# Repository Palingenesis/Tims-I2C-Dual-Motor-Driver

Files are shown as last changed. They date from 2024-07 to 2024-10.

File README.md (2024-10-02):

# This is My I2C Dual Motor Driver  
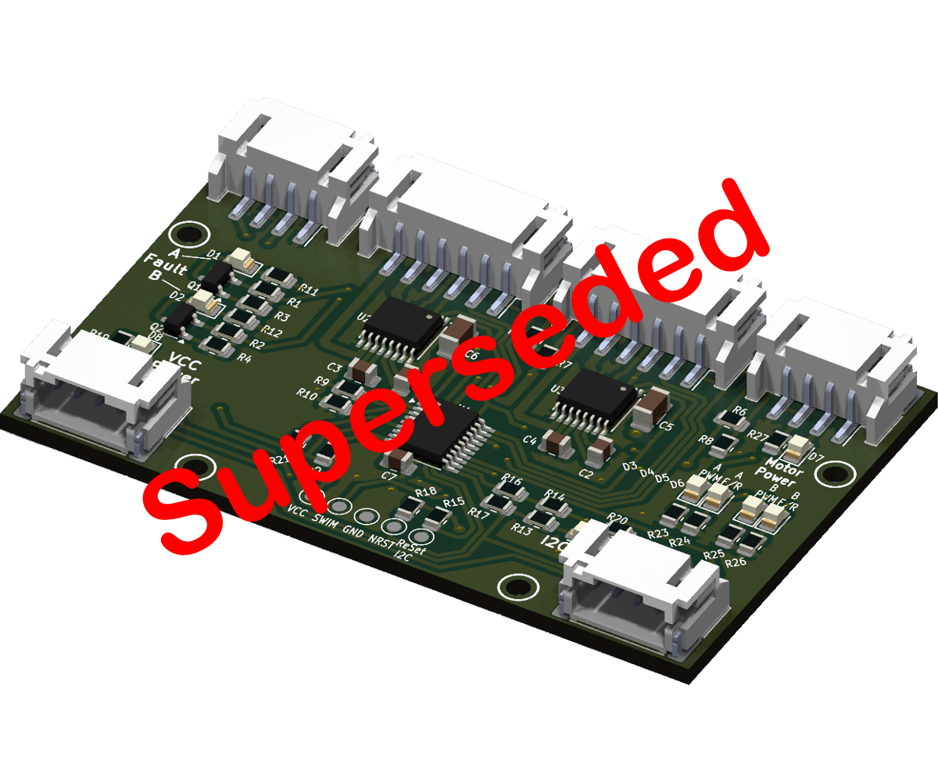
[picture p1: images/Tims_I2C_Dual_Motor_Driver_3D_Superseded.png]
3D Top
  
## This is an I2C controlled Dual Motor Driver Board.  
### This Board has been superseded by this one <a href="https://www.pcbway.com/project/shareproject/Tim_s_I2C_Dual_Motor_Driver_[Version_2]_0646aaaf.html">Tims I2C Dual Motor Driver Version 2</a>  
### Files are for [KiCAD EDA](https://www.kicad.org/)  
There is <span style="font-size: large;">**"Tims_I2C_Dual_Motor_Driver.kicad_pcb.zip"**</span> file  
* This can be used when **"Plot Files"** asked for at 
<sub></sub> 
when ordering 10 PCBs for $5  
* If you have <span style="font-size: large;">**[KiCAD EDA](https://www.kicad.org/)**</span>,  
<sub></sub>
have a Plugin Plugin that will make things simple to order a PCB,  
just load this project into <span style="font-size: large;">**[KiCAD EDA](https://www.kicad.org/)**</span> install the plugin click the Icon Plugin and it will create all the nesesery files needed and take you to order a PCB 
and compeate the form on 
<sub></sub> 
web site.  
  
<a href="https://www.pcbway.com/project/member/?bmbno=3B5E17AE-462C-47">PCB from PCBWay</a>
## About  
The board can control two motors with quadratic encoders and a station to set a reference point.  
This is my second I2C Motor Driver, My first worked OK, but The MOSFETS I used where a little temperamental,  
so I decided to make a more robust version.  
This one I decided to control 2 motors from one microcontroller.  
* The main reason for having it control two motors at the same time was that I tried my original motor drivers controlling a tracked vehicle.  
It worked fine with two single motor drivers  but because I was using a web interface to control them there was a delay between turning on/off each motor.  
* I thought having a motor driver that controls two motor at the same time was a better approach.  
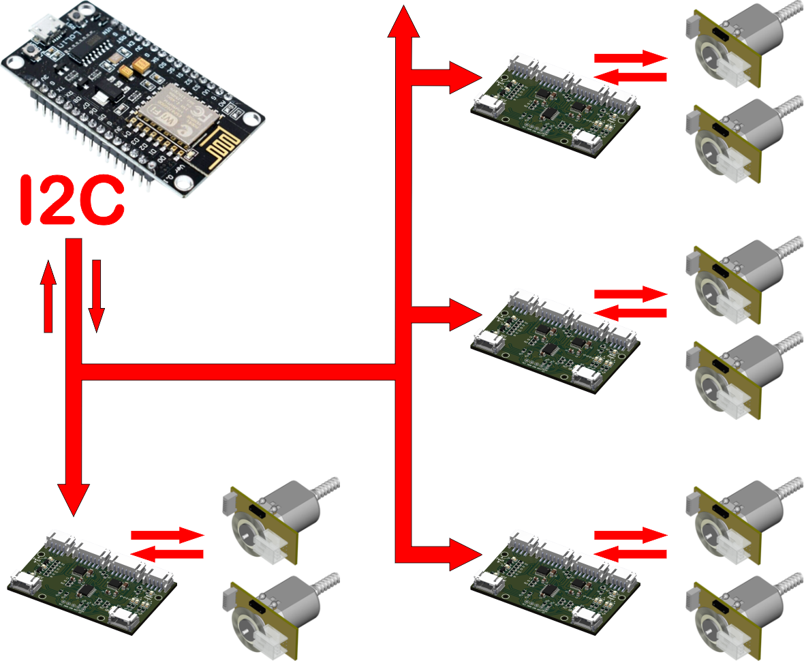
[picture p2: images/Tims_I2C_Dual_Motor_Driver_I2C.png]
I2C
  
## The Motor Driver is controlled via the I2C bus.  
* Each board can have its own unique I2C Address.  
* Not using the reserved Addresses over 100 in theory can be attached to one I2C bus. (Addresses 10 to 127 probably) 7-bit Address.  
* The is a system to reset the I2C default address to 0x30.  
* There are two sockets for the I2C to that the boards can be daisy-chained, end to end.  
* There is place for pull-up resistors, depending on muti-board setup or single board setup, these can be enabled/disabled.  
  
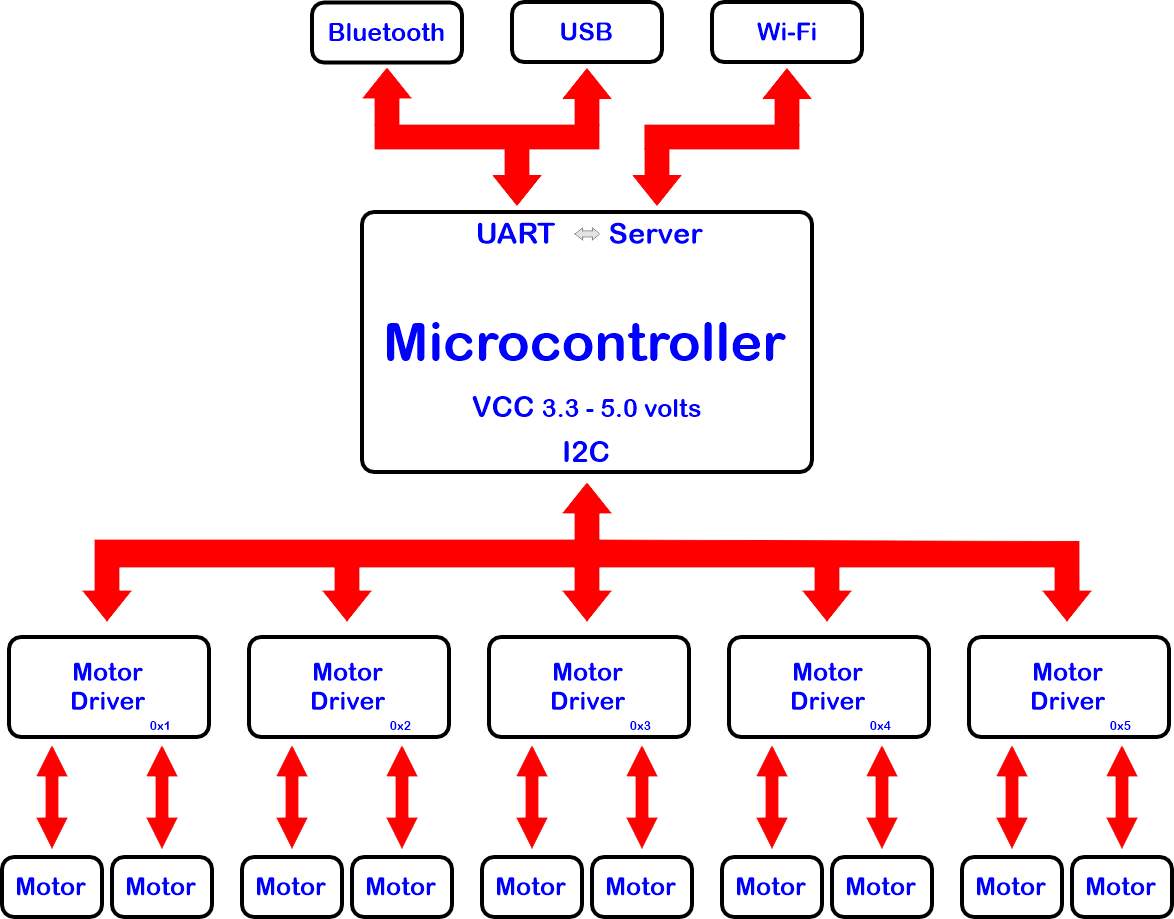
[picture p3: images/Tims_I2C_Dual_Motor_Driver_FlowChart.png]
Flow Chart
  
## The Microcontroller is the STM8S103F3
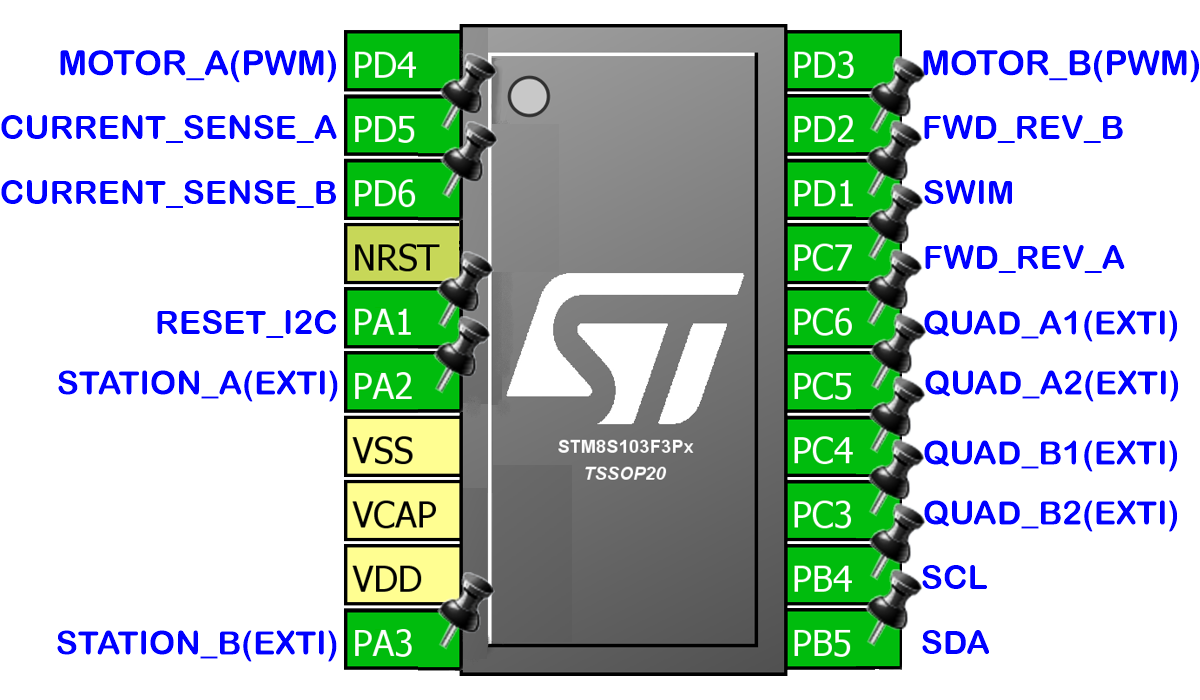
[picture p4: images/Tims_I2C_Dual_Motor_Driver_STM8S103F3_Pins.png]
STM8S103F3 Pins
  
* According to the Data Sheet, this can run with 2.95 to 5.5 V operating voltage.  
* Caution should be taken when programming, The ST-Link is 3.3v.  
* I was a little limited for pins and memory, as I am controlling two motors with this. The AI has been reduced, it still has inputs for quadratic encoders and a station, these enable it to know the rotation and position of the motors.  
* I was able to use the current sense from the DRV8876, so the load on the motors can be retrieved from communication via I2C.  
## There are LEDs for diagnostics.  
* Two Yellow LEDs, one for Motor Power and one for VCC.  
* There is a red LED on the SDA line to show activity.  
* For each motor there is a red LED to show a fault, a blue LED to show Motor on and a Green LED to show if motor forward or reverse (on/off).  
## There are Pads for programming the STM8S103F3
* To program the STM8S103F3 will require STMicroelectronics "ST Visual Programmer"  
* STMicroelectronics "ST Visual Programmer" is part of "ST MCU toolset".  
* I have done .s19 file for use with the "ST Visual Programmer".  
* An ST-Link is required.
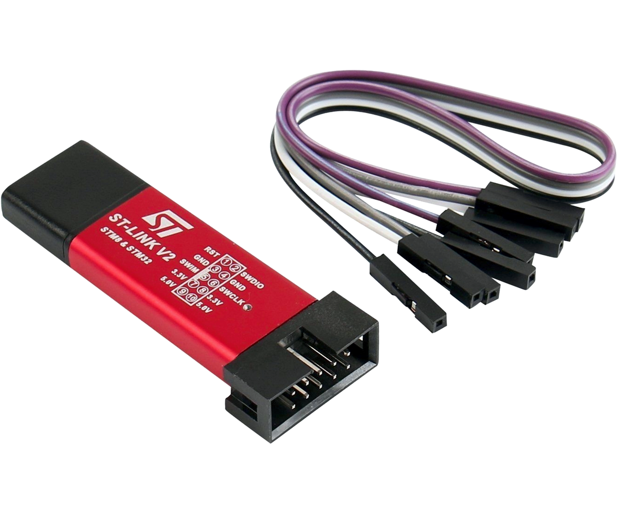
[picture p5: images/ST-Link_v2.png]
ST-Link_v2
  
## The Drivers used are DRV8876
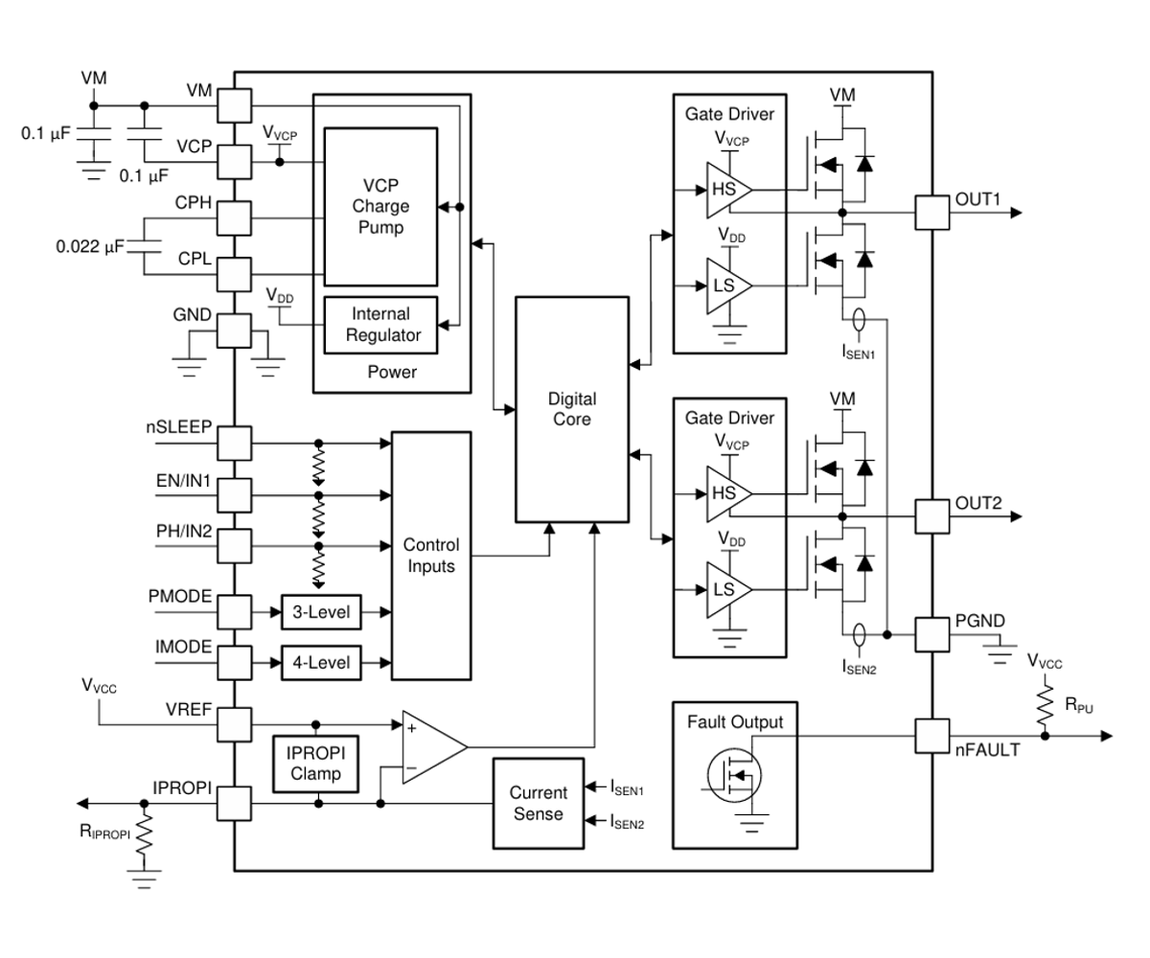
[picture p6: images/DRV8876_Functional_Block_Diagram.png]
DRV8876 Functional Block_Diagram
  
The DRV8876 is an N-channel H-bridge motor driver, the board has two of these.  
* They have 4.5-V to 37-V operating supply voltage range.  
* 3.5-A Peak. On the board I have put places for Current limit resistors.  
* Supports 1.8-V, 3.3-V, and 5-V logic inputs. (The STM8S103F3 opperates at 2.95 to 5.5 V)  
* On the board the DRV8876 are set to PH/EN Control Mode.  
* The nSleep is fixed High, so no low power mode.  
* I have connected the IPROPI to the STM8S103F3 so current readings can be sensed.  
## There are connections for a Quadratic Encoder for each Motor  
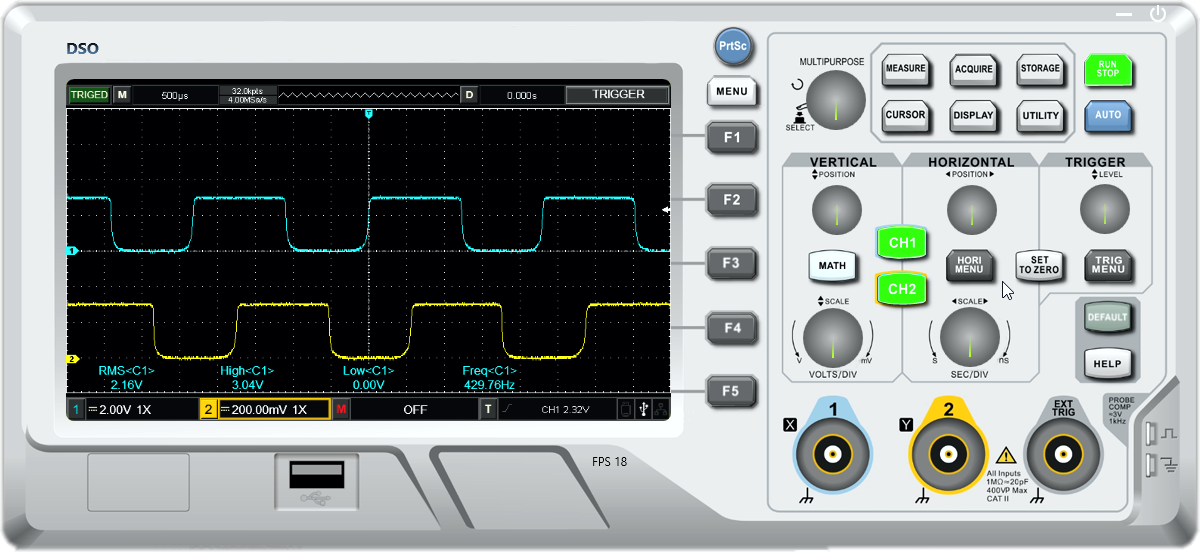
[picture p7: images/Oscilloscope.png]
Quadratic Signal
  
The Quadratic Encoder needs to be the A/B type and be the same VCC as the Board.  
* If the Board counts bacwards when the motor runs forward, the two quadratic input need to be swapped.  
* With an encoder attached to a motor, commands can be sent to set the motor to a specific position.  
## There are connections for a Station for each Motor  
* A Station is a place for a switch to be fitted to a project, that when triggerd, will reset the position of the Motor to a known position.  
* There are two settings for the station depending on the direction of the Motor, most switches don't trigger at the same point when turning on and off.  
## Commands  
The Motor Driver Board is controlled by commands on the I2C Bus.  
* The Board can be connected to any microcontroller that has I2C.  
* All commands start with any byte, this is because I have an ESP8266 and they haven't fixed the first data byte issue. When sending data via the I2C on the ESP8266 the first byte gets 0x80 added to it. So my driver ignores the first byte sent. For simplicity I will use '#' as the first character of all commands sent to the Motor Driver.  
* The second byte is the Identifier that tells the driver the type of command. All commands are from the second byte onwards. I should say "char" as all commands are sent as ASCII characters.  
## Global Command 'M'  
* **M1** = Motor A is the current motor that will be adjusted.  
* **M2** = Motor B is the current motor that will be adjusted.  
* **M3** = Motor A and B be adjusted.  
* A global command can be used on its own (preceded with '#') or at the end of other commands (preceded with a space)  
## 'C' Commands (settings):
* **C1** = Sets the Current Position to 0 (zero). Just use **C1**.  
* **C6 B\<value>** = Set: Has a Station Position. **B**oolean = 1 or 0 (true or false).  
* **C7 P\<value>** = Set the Forward Station **P**osition value. value = a 16 bit value, Sets the Station Position while moving Forward.  
* **C8 P\<value>** = Set the Reverse Station **P**osition value. value = a 16 bit value, Sets the Station Position while moving in Reverse.  
* **C10 A\<value>** = Set I2C **A**ddress. value = 1 (0x00) to 127 (0x7F). This is to change the I2C Address of the device.  
* **C13 B\<value>** = Set I2C Speed. **B**oolean; Is it 400k. value = 1 or 0 (true or false). 1 = 400000, 0 = 100000.  
All setting are saved in non volatile memory.  
* No need to apply settings every time power it connected.  
## 'S' Command (Speed):
**S\<Value>** = Set the **S**peed 0 to 1000. This is a PWM value. So 500 would be 50% on 50% off square wave.  
## 'F' Commands (Forward):
* **F0** = Stop. Can just use 'F' as the buffer will be full of zeros.  
* **F1** = Forward at a current Speed.  
* **F1 S\<value>** = Forward at a set Speed.  
## 'R' Commands (Reverse):  
* **R0** = Stop. Can just use 'R' as the buffer will be full of zeros.  
* **R1** = Reverse at a current Speed.  
* **R1** S<value> = Reverse at a set Speed.  
## 'G' Commands (Go to):
* **G0** = **Stop**. Can just use **'G'** as the buffer will be full of zeros.  
* **G1 P\<value> S\<value>** = Move to an absolute **P**osition Forward (Positive) of zero at a **S**peed.  
* **G2 P\<value> S\<value>** = Move to an absolute **P**osition Reverse (Negative) of zero at a **S**peed.  
  
*Settings that set a position are only valid with motors that have a Quadratic Encoder.*  
  
The **'G'** code **P**\<value> can be negative values. So why have **G1** and **G2**?  
* To keep options open.  
* All positions are relative to a zero.  
* When writing your own code to control the Motors you may only have the option of Unsigned Integers.  
* You may want to only use Unsigned Integers to save memory.  

### *Click this image to see a video of it in use.*
[](https://www.youtube.com/watch?v=bSmED1MQUrw)

## A Typical 4 Motor setup  
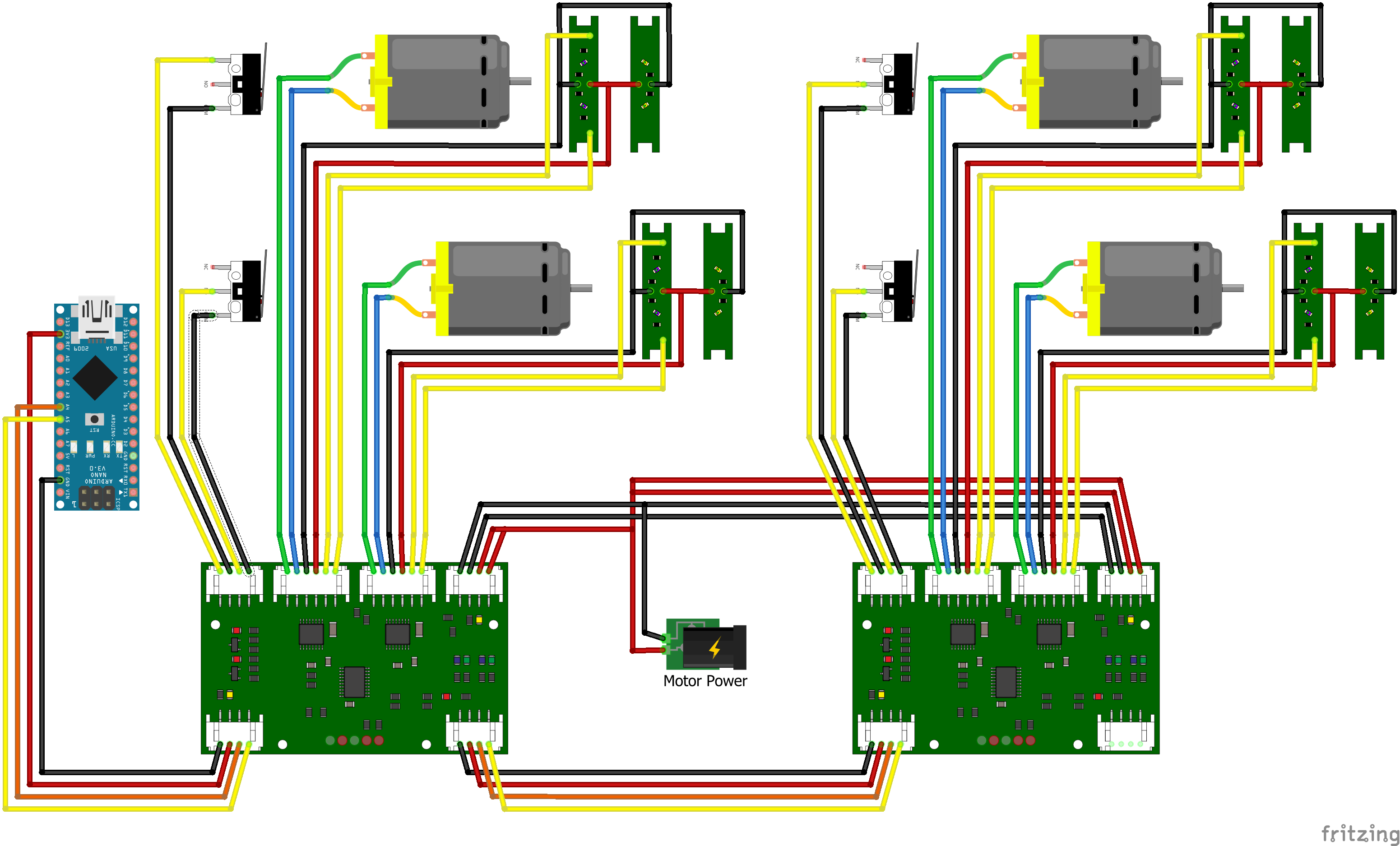
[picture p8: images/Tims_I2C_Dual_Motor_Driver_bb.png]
Typical 4 Motor setup
  
* One Microcontroller.  
* Two Driver Boards.  
* Four Motors With Quadratic Encoders.  
* Each Motor has a Station to set the the zero position.

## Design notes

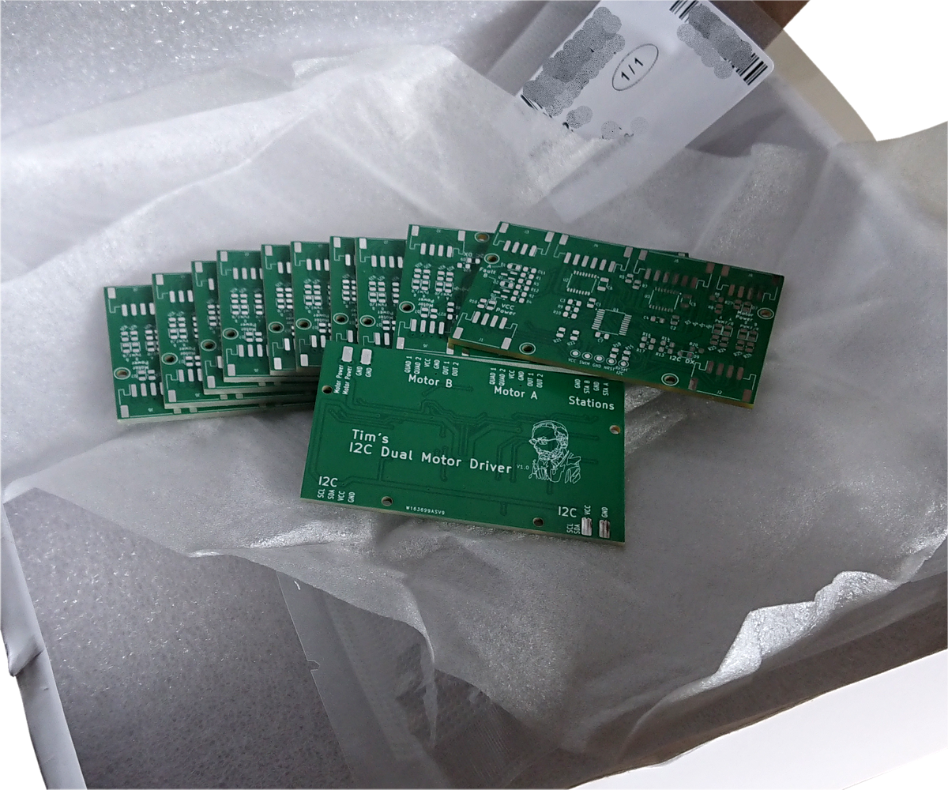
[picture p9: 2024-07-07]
images/Tims_I2C_Dual_Motor_Driver (Delivery).png

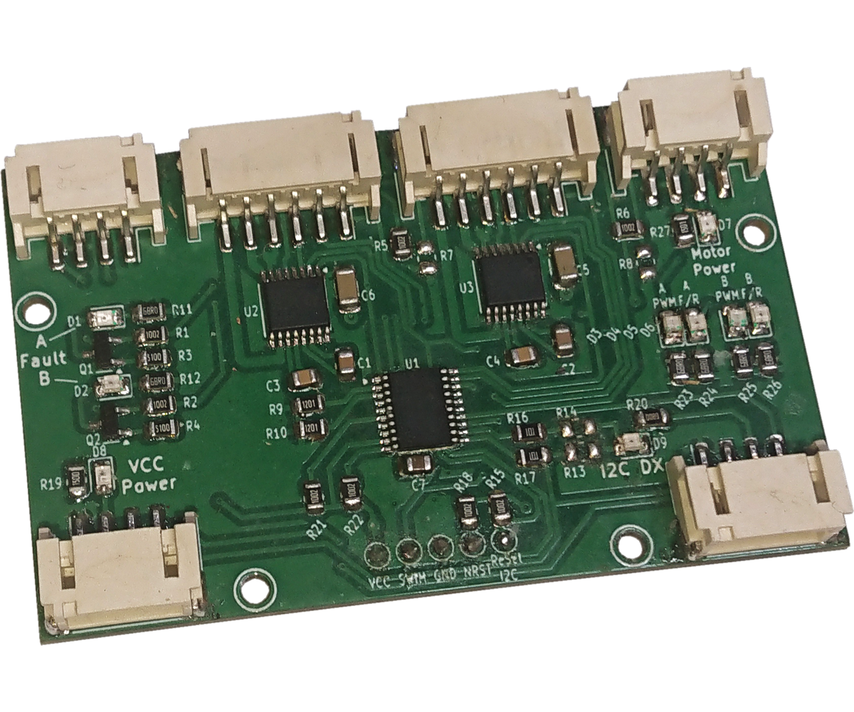
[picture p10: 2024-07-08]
images/Tims I2C Dual_Motor_Driver_Finished_Photo.png

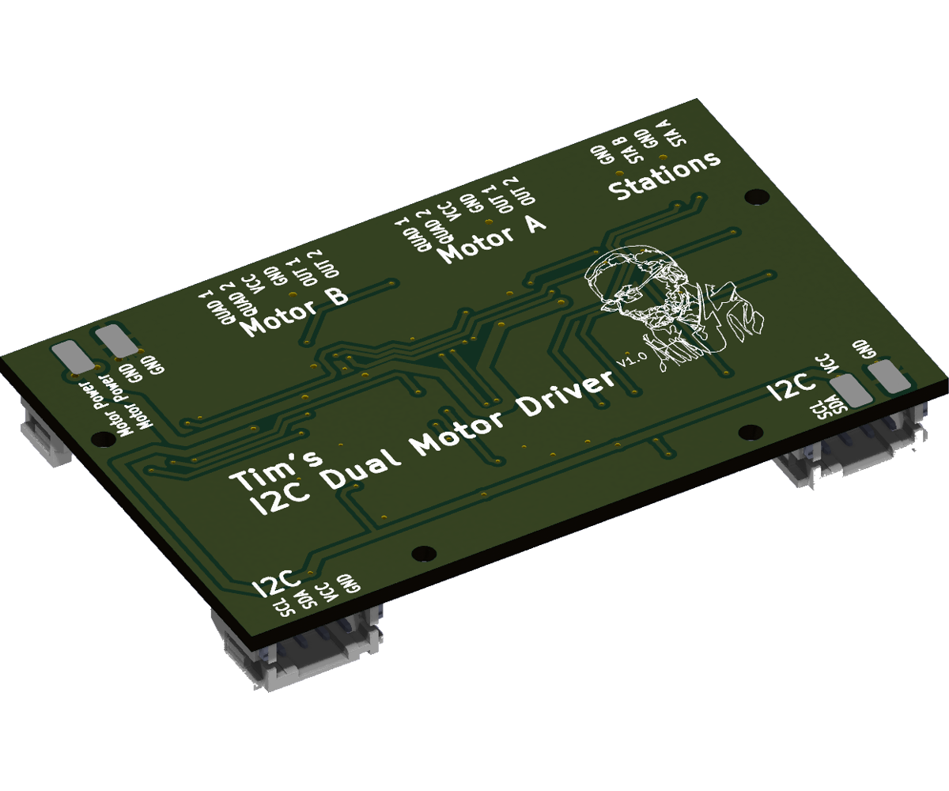
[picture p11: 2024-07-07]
images/Tims_I2C_Dual_Motor_Driver (3D Bottom).png

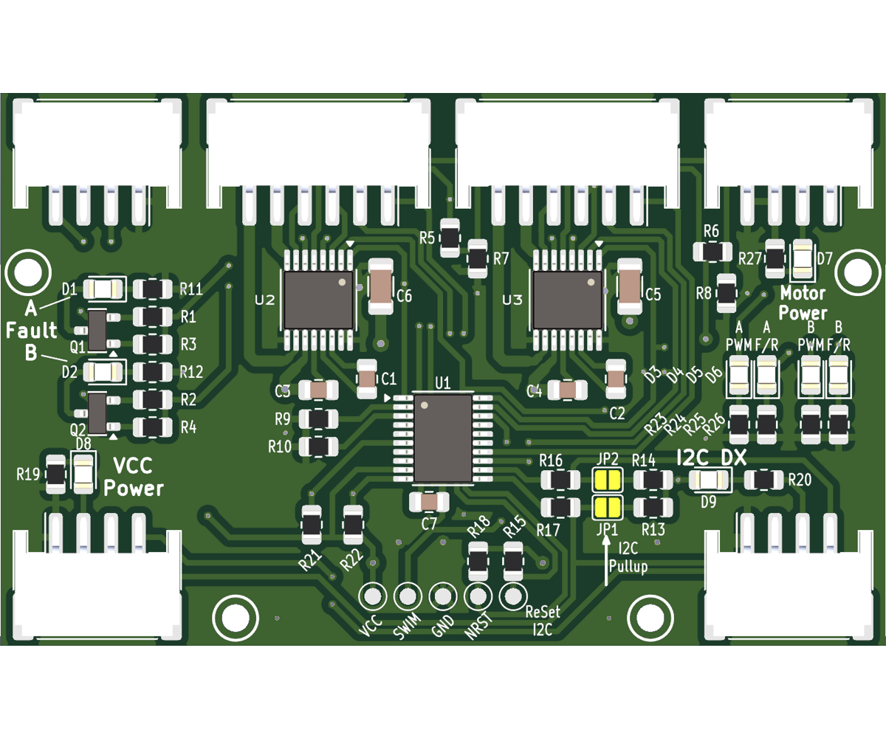
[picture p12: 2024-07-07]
images/Tims_I2C_Dual_Motor_Driver (Top).png

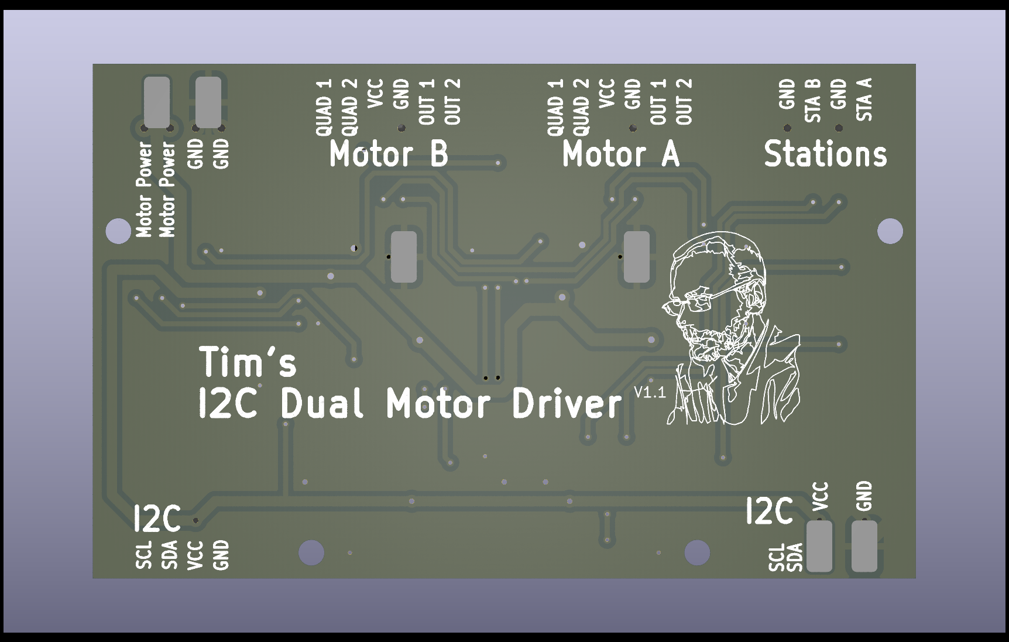
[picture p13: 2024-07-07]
images/Tims_I2C_Dual_Motor_Driver (Ren Bottom).png

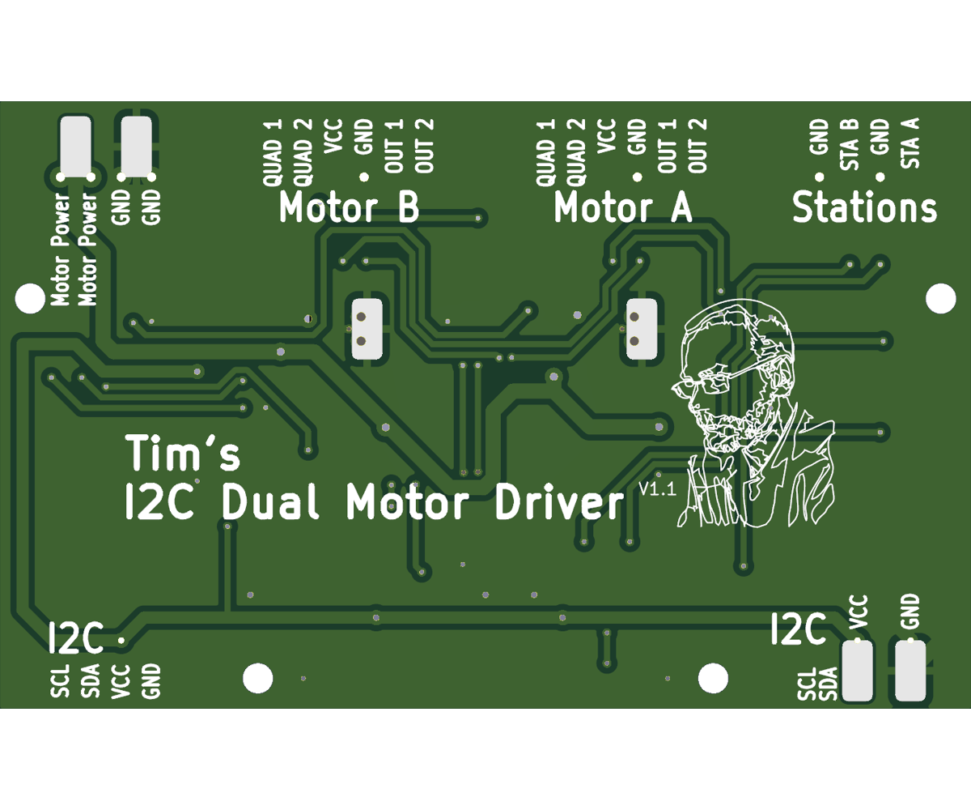
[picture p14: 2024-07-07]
images/Tims_I2C_Dual_Motor_Driver (Bottom).png

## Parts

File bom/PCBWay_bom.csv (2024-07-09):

designator | quantity | value | pack | mpn | mount_type
C1, C2 | 2 | 22nF | C_0805_2012Metric |  | smt
C3, C4 | 2 | 100nF | C_0805_2012Metric |  | smt
C5, C6 | 2 | 100nF | C_1206_3216Metric |  | smt
C7 | 1 | 1uF | C_0805_2012Metric |  | smt
D1, D2, D9 | 3 | LED (Red) | LED_0805_2012Metric |  | smt
D3, D5 | 2 | LED (Blue) | LED_0805_2012Metric |  | smt
D4, D6 | 2 | LED (Green) | LED_0805_2012Metric |  | smt
D7, D8 | 2 | LED (Yellow) | LED_0805_2012Metric |  | smt
J1, J2 | 2 | I2C | JST_PH_S4B-PH-SM4-TB_1x04-1MP_P2.00mm_Horizontal |  | smt
J3 | 1 | Stations | JST_PH_S4B-PH-SM4-TB_1x04-1MP_P2.00mm_Horizontal |  | smt
J4 | 1 | Motor A | JST_PH_S6B-PH-SM4-TB_1x06-1MP_P2.00mm_Horizontal |  | smt
J5 | 1 | Motor B | JST_PH_S6B-PH-SM4-TB_1x06-1MP_P2.00mm_Horizontal |  | smt
J6 | 1 | Motor Power | JST_PH_S4B-PH-SM4-TB_1x04-1MP_P2.00mm_Horizontal |  | smt
JP1, JP2 | 2 | Pull Up | SolderJumper-2_P1.3mm_Open_RoundedPad1.0x1.0mm |  | tht
Pad1 | 1 | VCC | Wire_Pad_D1.2mm |  | smt
Pad10, Pad11 | 2 | Heat Sink | Wire_Pad_2050mm |  | smt
Pad2 | 1 | SWIM | Wire_Pad_D1.2mm |  | smt
Pad3 | 1 | GND | Wire_Pad_D1.2mm |  | smt
Pad4 | 1 | NRST | Wire_Pad_D1.2mm |  | smt
Pad5 | 1 | Reset I2C | Wire_Pad_D1.2mm |  | smt
Pad6 | 1 | VCC | Wire_Pad_2050mm |  | smt
Pad7, Pad9 | 2 | GND | Wire_Pad_2050mm |  | smt
Pad8 | 1 | Motor power | Wire_Pad_2050mm |  | smt
Q1, Q2 | 2 | PNP_S8550 | SOT-23 |  | smt
R1, R15, R18, R2, R21, R22, R5, R6 | 8 | 10k | R_0805_2012Metric |  | smt
R10, R9 | 2 | 1k3 | R_0805_2012Metric |  | smt
R11, R12, R23, R24, R25, R26 | 6 | 68R | R_0805_2012Metric |  | smt
R13, R14 | 2 | 4k7 | R_0805_2012Metric |  | smt
R16, R17 | 2 | 100R | R_0805_2012Metric |  | smt
R19 | 1 | 150R | R_0805_2012Metric |  | smt
R20 | 1 | 680R | R_0805_2012Metric |  | smt
R27 | 1 | 1K5 | R_0805_2012Metric |  | smt
R3, R4 | 2 | 510R | R_0805_2012Metric |  | smt
R7, R8 | 2 | Omit | R_0805_2012Metric |  | smt
U1 | 1 | STM8S103F | TSSOP-20_4.4x6.5mm_P0.65mm |  | smt
U2, U3 | 2 | DRV8876 | HTSSOP-16-1EP_4.4x5mm_P0.65mm_EP3x3mm |  | smt

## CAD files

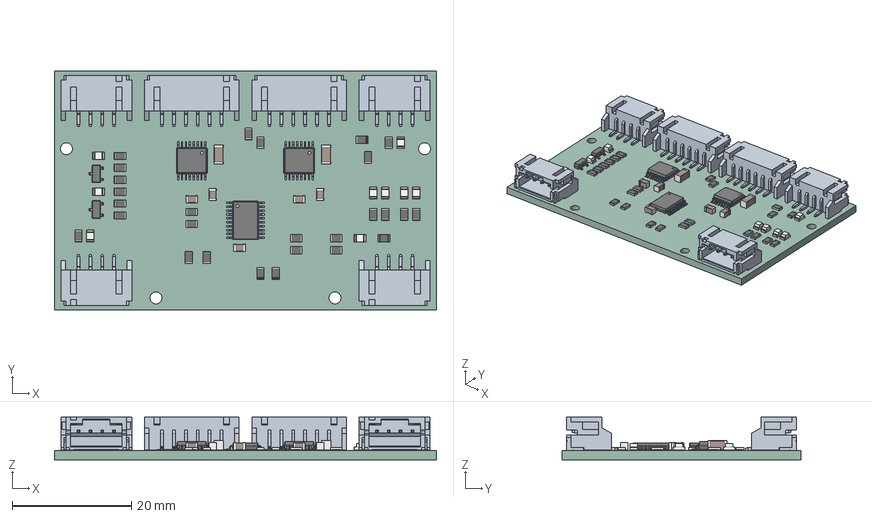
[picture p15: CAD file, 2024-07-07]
Tims_I2C_Dual_Motor_Driver_NoTracks.step
64.0 x 40.0 x 7.15 mm
R_0805_2012Metric x 27
SSOP_16_44x52mm_P065mm x 2
C_0805_2012Metric x 5
LED_0805_2012Metric x 9
SxBwhite4 x 4
TSSOP_20_44x65mm_P065mm
SxBwhite6 x 2
C_1206_3216Metric x 2
SOT_23 x 2
_autosave-Tims_I2C_Dual_Motor_Driver_PCB

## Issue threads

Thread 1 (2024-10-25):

I think I’ve finally found my teacher!

Tpj-root, 2024-10-25:
Professor, I have a lot of questions. If you have free time, could you please correct my mistakes? I'd like to tell you about my projects. Could you share your email address? If not, no worries—I don’t want to bother you.

Thank you!

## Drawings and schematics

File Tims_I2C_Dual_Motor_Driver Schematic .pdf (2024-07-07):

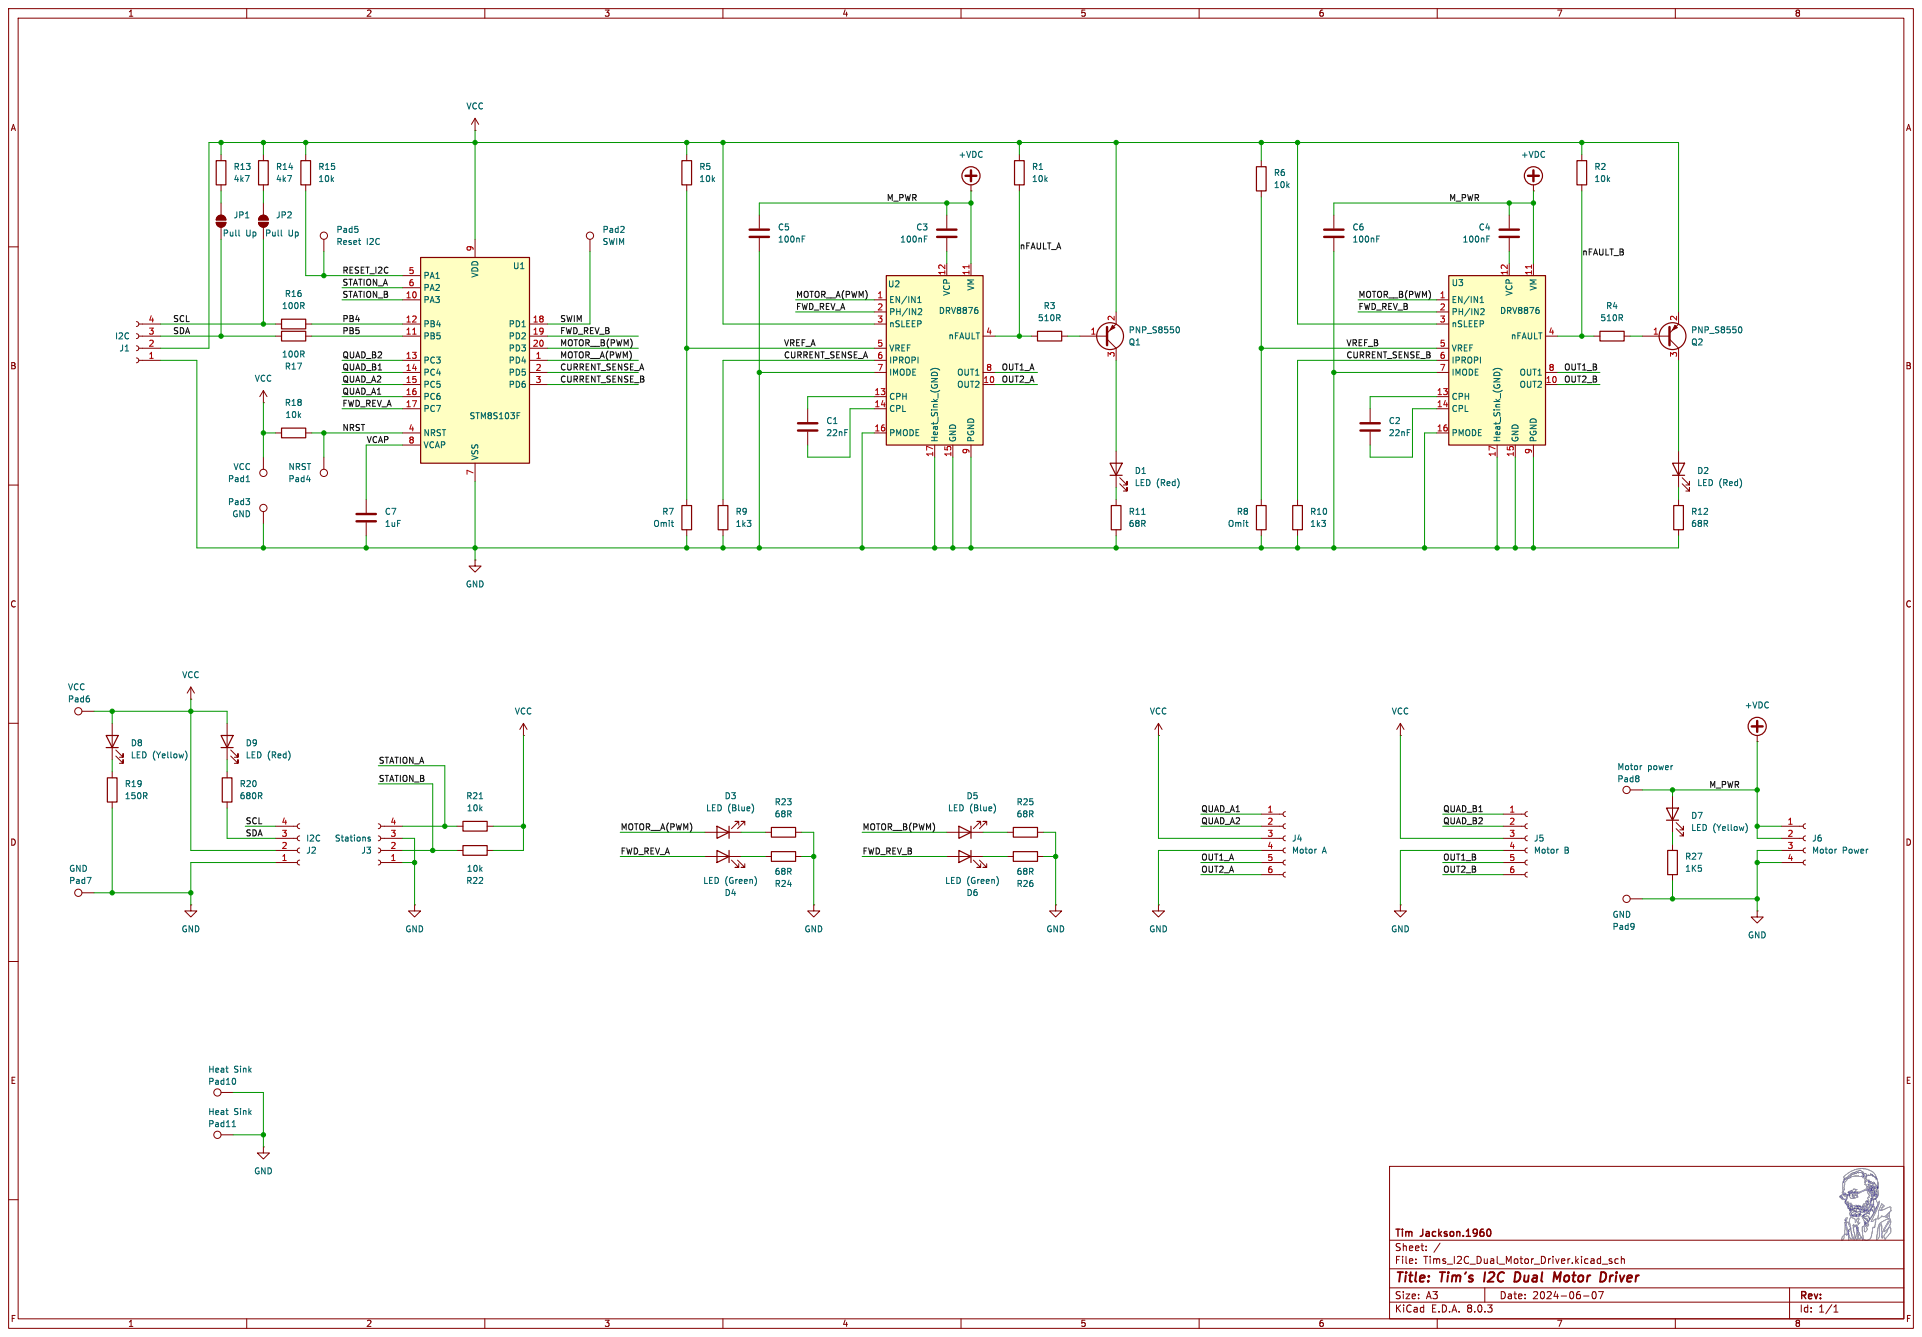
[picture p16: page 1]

LED (Yellow) Pad8 Motor power R11

Id: 1/1 Title: Tim's I2C Dual Motor Driver File: Tims_I2C_Dual_Motor_Driver.kicad_sch Sheet: / Tim Jackson.1960

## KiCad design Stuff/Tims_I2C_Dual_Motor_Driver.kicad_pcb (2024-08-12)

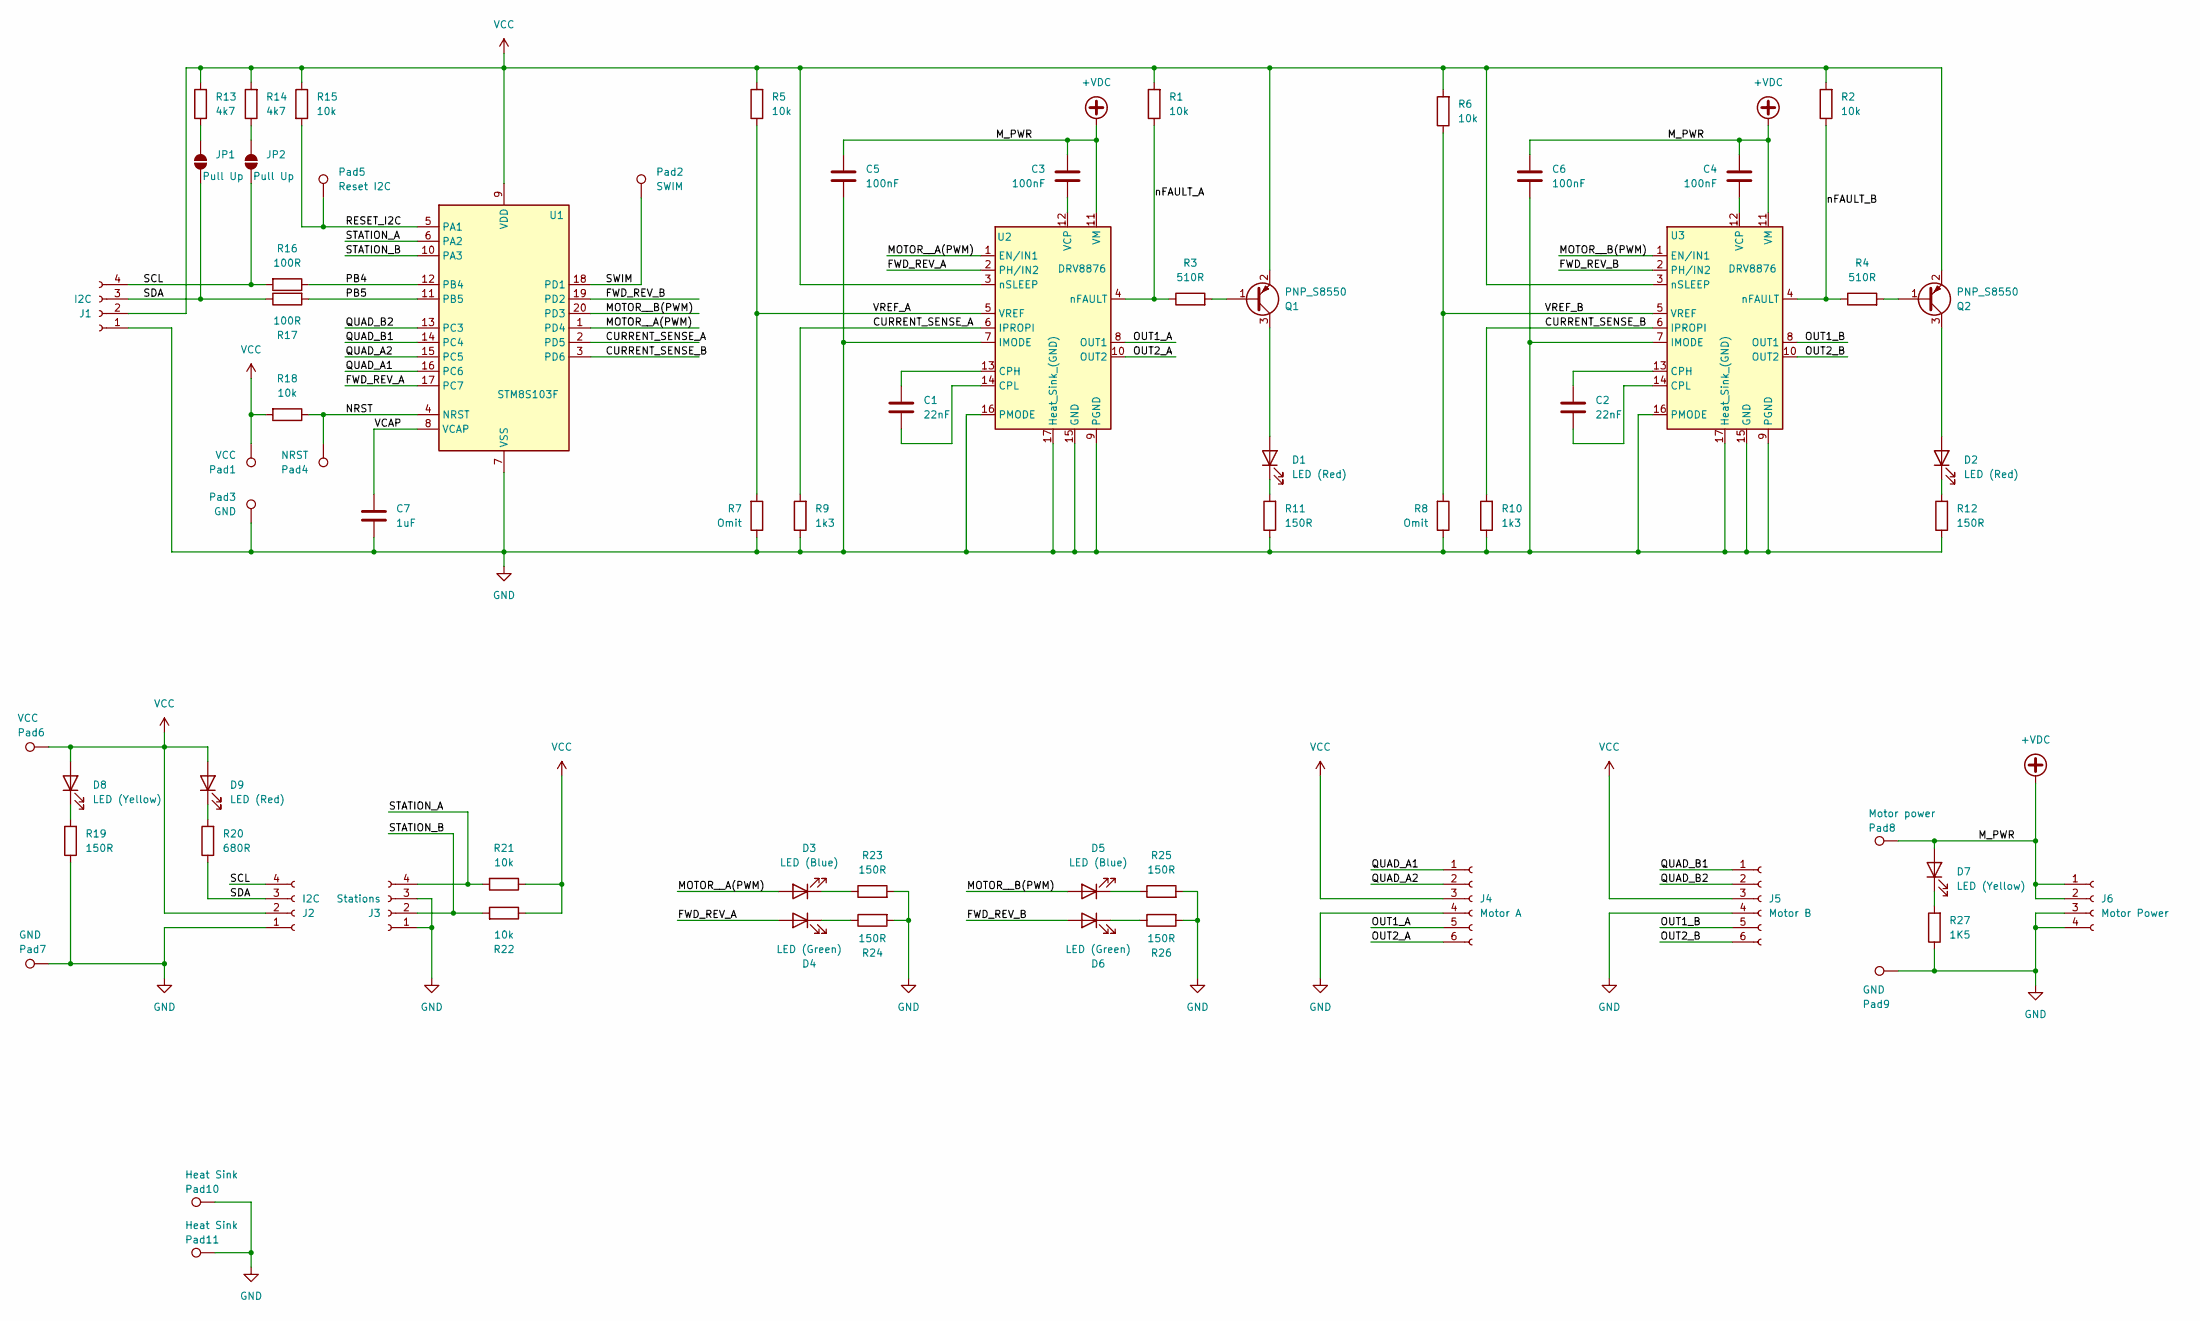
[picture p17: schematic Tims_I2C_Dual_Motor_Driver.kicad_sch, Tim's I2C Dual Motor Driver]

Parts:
C1, C2: 22nF; C_0805_2012Metric
C3, C4: 100nF; C_0805_2012Metric
C5, C6: 100nF; C_1206_3216Metric
C7: 1uF; C_0805_2012Metric
D1, D2, D9: LED (Red); LED_0805_2012Metric
D3, D5: LED (Blue); LED_0805_2012Metric
D4, D6: LED (Green); LED_0805_2012Metric
D7, D8: LED (Yellow); LED_0805_2012Metric
J1, J2: I2C; JST_PH_S4B-PH-SM4-TB_1x04-1MP_P2.00mm_Horizontal
J3: Stations; JST_PH_S4B-PH-SM4-TB_1x04-1MP_P2.00mm_Horizontal
J4: Motor A; JST_PH_S6B-PH-SM4-TB_1x06-1MP_P2.00mm_Horizontal
J5: Motor B; JST_PH_S6B-PH-SM4-TB_1x06-1MP_P2.00mm_Horizontal
J6: Motor Power; JST_PH_S4B-PH-SM4-TB_1x04-1MP_P2.00mm_Horizontal
JP1, JP2: Pull Up; SolderJumper-2_P1.3mm_Open_RoundedPad1.0x1.0mm
Pad1: VCC; Wire_Pad_D1.2mm
Pad2: SWIM; Wire_Pad_D1.2mm
Pad3: GND; Wire_Pad_D1.2mm
Pad4: NRST; Wire_Pad_D1.2mm
Pad5: Reset I2C; Wire_Pad_D1.2mm
Pad6: VCC; Wire_Pad_2050mm
Pad7, Pad9: GND; Wire_Pad_2050mm
Pad8: Motor power; Wire_Pad_2050mm
Pad10, Pad11: Heat Sink; Wire_Pad_2050mm
Q1, Q2: PNP_S8550; SOT-23
R1, R2, R5, R6, R15, R18, R21, R22: 10k; R_0805_2012Metric
R3, R4: 510R; R_0805_2012Metric
R7, R8: Omit; R_0805_2012Metric
R9, R10: 1k3; R_0805_2012Metric
R11, R12, R19, R23, R24, R25, R26: 150R; R_0805_2012Metric
R13, R14: 4k7; R_0805_2012Metric
R16, R17: 100R; R_0805_2012Metric
R20: 680R; R_0805_2012Metric
R27: 1K5; R_0805_2012Metric
U1: STM8S103F; TSSOP-20_4.4x6.5mm_P0.65mm
U2, U3: DRV8876; HTSSOP-16-1EP_4.4x5mm_P0.65mm_EP3x3mm

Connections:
+VDC: C3.2, C4.2, C5.1, C6.1, D7.2 (A), J6.1, J6.2, Pad8.1, U2.11 (VM), U3.11 (VM)
/CURRENT_SENSE_A: R9.2, U1.2 (PD5), U2.6 (IPROPI)
/CURRENT_SENSE_B: R10.2, U1.3 (PD6), U3.6 (IPROPI)
/FWD_REV_A: D4.2 (A), U1.17 (PC7), U2.2 (PH/IN2)
/FWD_REV_B: D6.2 (A), U1.19 (PD2), U3.2 (PH/IN2)
/MOTOR__A(PWM): D3.2 (A), U1.1 (PD4), U2.1 (EN/IN1)
/MOTOR__B(PWM): D5.2 (A), U1.20 (PD3), U3.1 (EN/IN1)
/NRST: Pad4.1, R18.1, U1.4 (NRST)
/OUT1_A: J4.5, U2.8 (OUT1)
/OUT1_B: J5.5, U3.8 (OUT1)
/OUT2_A: J4.6, U2.10 (OUT2)
/OUT2_B: J5.6, U3.10 (OUT2)
/PB4: R16.1, U1.12 (PB4)
/PB5: R17.2, U1.11 (PB5)
/QUAD_A1: J4.1, U1.16 (PC6)
/QUAD_A2: J4.2, U1.15 (PC5)
/QUAD_B1: J5.1, U1.14 (PC4)
/QUAD_B2: J5.2, U1.13 (PC3)
/RESET_I2C: Pad5.1, R15.2, U1.5 (PA1)
/SCL: J1.4, J2.4, JP2.1 (A), R16.2
/SDA: J1.3, J2.3, JP1.1 (A), R17.1, R20.1
/STATION_A: J3.4, R21.2, U1.6 (PA2)
/STATION_B: J3.2, R22.2, U1.10 (PA3)
/SWIM: Pad2.1, U1.18 (PD1)
/VCAP: C7.1, U1.8 (VCAP)
/VREF_A: R5.1, R7.2, U2.5 (VREF)
/VREF_B: R6.1, R8.2, U3.5 (VREF)
/nFAULT_A: R1.1, R3.1, U2.4 (nFAULT)
/nFAULT_B: R2.1, R4.1, U3.4 (nFAULT)
GND: C5.2, C6.2, C7.2, J1.1, J2.1, J3.1, J3.3, J4.4, J5.4, J6.3, J6.4, Pad3.1, Pad7.1, Pad9.1, Pad10.1, Pad11.1, R7.1, R8.1, R9.1, R10.1, R11.1, R12.1, R19.1, R23.2, R24.2, R25.2, R26.2, R27.1, U1.7 (VSS), U2.7 (IMODE), U2.9 (PGND), U2.15 (GND), U2.16 (PMODE), U2.17 (Heat_Sink_(GND)), U3.7 (IMODE), U3.9 (PGND), U3.15 (GND), U3.16 (PMODE), U3.17 (Heat_Sink_(GND))
unnamed: D1.2 (A), Q1.3 (C)
unnamed: D1.1 (K), R11.2
unnamed: D2.2 (A), Q2.3 (C)
unnamed: D2.1 (K), R12.2
unnamed: D3.1 (K), R23.1
unnamed: D4.1 (K), R24.1
unnamed: D5.1 (K), R25.1
unnamed: D6.1 (K), R26.1
unnamed: D7.1 (K), R27.2
unnamed: D8.1 (K), R19.2
unnamed: D9.1 (K), R20.2
unnamed: JP1.2 (B), R13.1
unnamed: JP2.2 (B), R14.1
unnamed: Q1.1 (B), R3.2
unnamed: Q2.1 (B), R4.2
unnamed: C1.1, U2.13 (CPH)
unnamed: C1.2, U2.14 (CPL)
unnamed: C3.1, U2.12 (VCP)
unnamed: C2.1, U3.13 (CPH)
unnamed: C2.2, U3.14 (CPL)
unnamed: C4.1, U3.12 (VCP)
VCC: D8.2 (A), D9.2 (A), J1.2, J2.2, J4.3, J5.3, Pad1.1, Pad6.1, Q1.2 (E), Q2.2 (E), R1.2, R2.2, R5.2, R6.2, R13.2, R14.2, R15.1, R18.2, R21.1, R22.1, U1.9 (VDD), U2.3 (nSLEEP), U3.3 (nSLEEP)

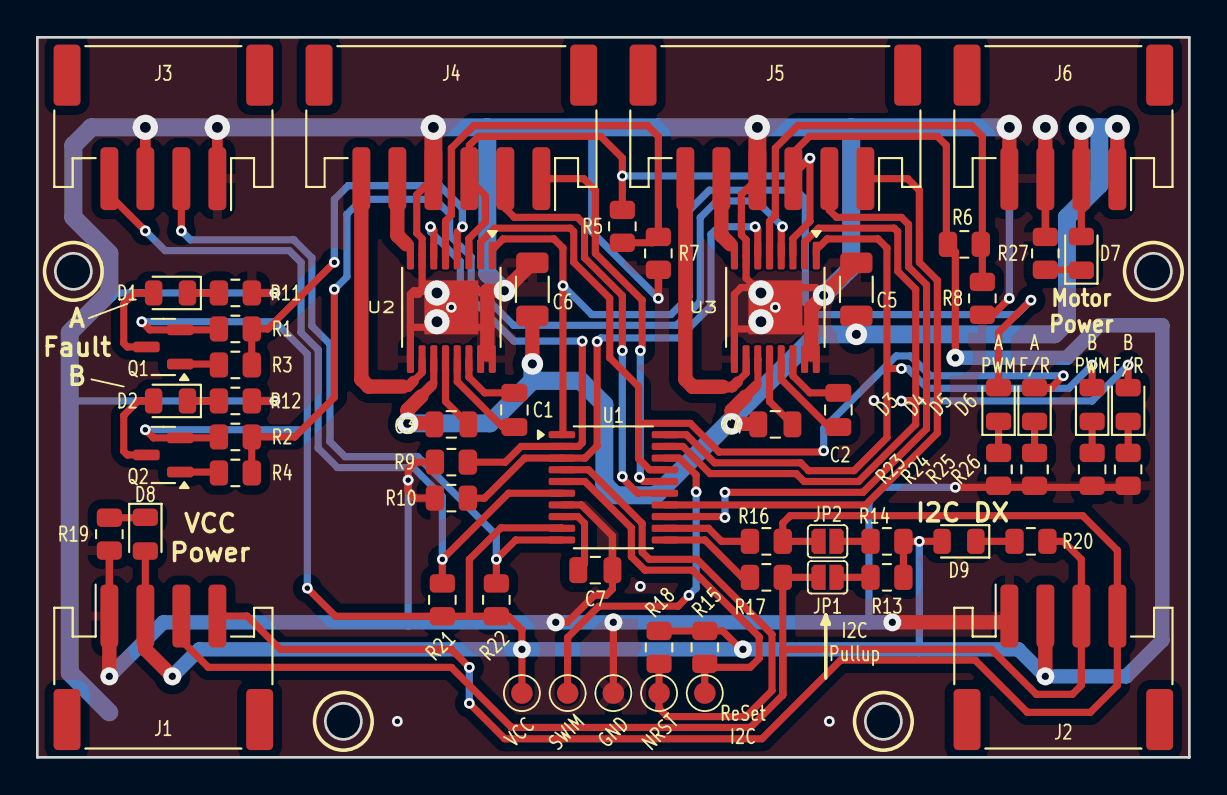
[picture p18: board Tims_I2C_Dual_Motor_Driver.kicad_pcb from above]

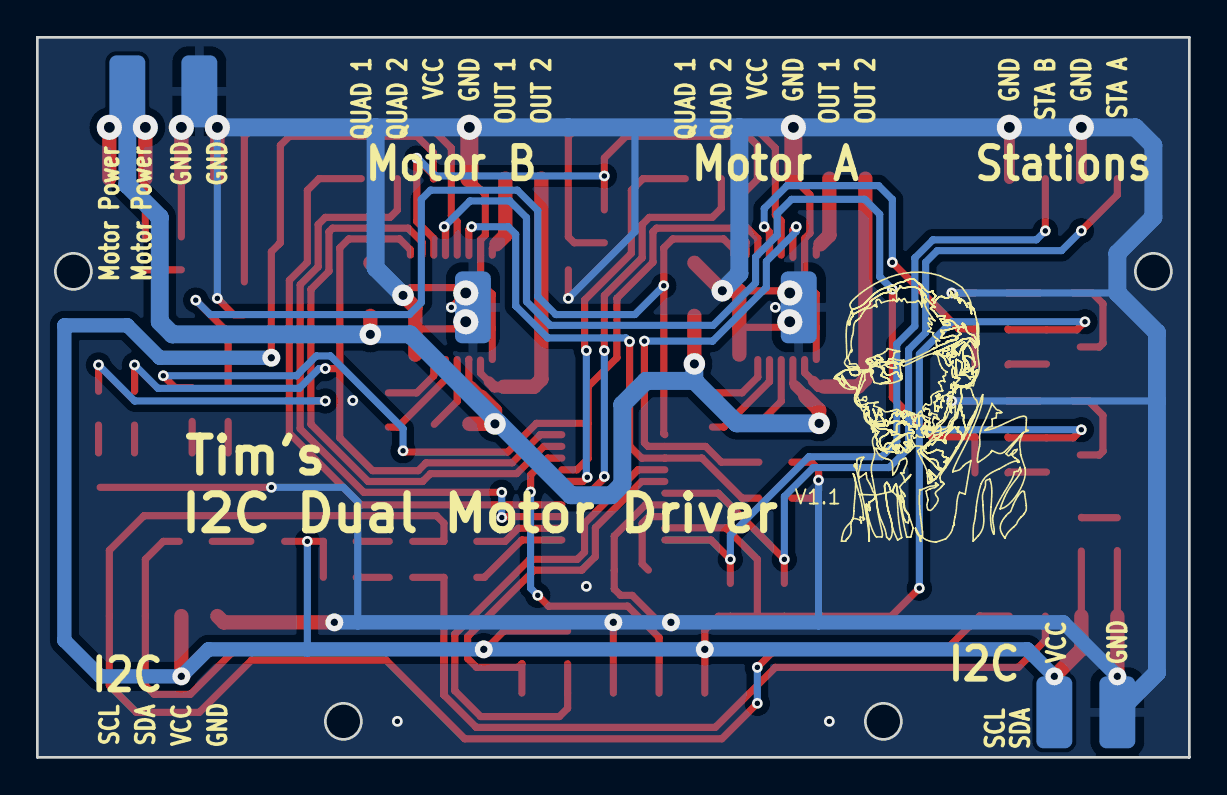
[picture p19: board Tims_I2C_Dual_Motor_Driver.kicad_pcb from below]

Board: 2 copper layers, 64.0 x 40.0 mm, 67 parts (6 on the bottom side), 52 nets.

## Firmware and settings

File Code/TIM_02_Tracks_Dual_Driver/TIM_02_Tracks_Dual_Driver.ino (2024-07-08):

/*
	This is code to control the tracks of my robot TIM-02.

	By Tim Jackson.1960
		More info on Instructables. https://www.instructables.com/member/Palingenesis/instructables/

	This Sketch was written for the ESP8266 (new NodeMCU). V1.0

	Wire request buffer of the Motor Driver was originaly set/configured for 32 bit values but was reduced to 24+ bit numbers.
	The original code is commented out should I change microcontroller with more memory.
	I say 24+ bit number becouse I have used a seperate Byte for negative flags.
	This gives a number range of: -16,777,215 to 16,777,215.
	To make it more universal, all values are Ticks of the Motors Quadratic Encoder.

	Wire_Request converts as follows:

	Flags	(2 bytes Used to hold 16 single bit values like negative switches and flags)

	First Byte:
		Flags_1 true if:
			LSB		1	=	0x01 	CurPosition_A < 0
					2	=	0x02	CurPosition_B < 0
					4	=	0x04	Station_F_A < 0
					8	=	0x08	Station_F_B < 0
					16	=	0x10	Station_R_A < 0
					32	=	0x20	Station_R_B < 0
					64	=	0x40	Has_Station_A
			MSB		128	=	0x80	Has_Station_B

	Second Byte:
		Flags_2 true if:
			LSB		1	=	0x01	Debug Value 1 < 0
					2	=	0x02	Debug Value 2 < 0
					4	=	0x04	Is_400K (default = 100K)
					8	=	0x08
					16	=	0x10
					32	=	0x20
					64	=	0x40
			MSB		128	=	0x80

		Bytes 2 to 7	(3 bytes = 24 Bit):
			CurPossition_A	_Val_32 & 0xFF
			CurPossition_A	(_Val_32 >> 8) & 0xFF
			CurPossition_A	(_Val_32 >> 16) & 0xFF
			CurPossition_B	_Val_32 & 0xFF
			CurPossition_B	(_Val_32 >> 8) & 0xFF
			CurPossition_B	(_Val_32 >> 16) & 0xFF

		Byte 8	(1 byte = 8 Bit):
			I2C_Address

		Bytes 9 to 16	(2 bytes = 16 Bit):
			Station_F_A		_Val_32 & 0xFF
			Station_F_A		(_Val_32 >> 8) & 0xFF
			Station_F_B		_Val_32 & 0xFF
			Station_F_B		(_Val_32 >> 8) & 0xFF
			Station_R_A		_Val_32 & 0xFF
			Station_R_A		(_Val_32 >> 8) & 0xFF
			Station_R_B		_Val_32 & 0xFF
			Station_R_B		(_Val_32 >> 8) & 0xFF

		Bytes 17 to 20	(2 bytes = 16 Bit):
			Motor Load A	_Val_32 & 0xFF
			Motor Load A	(_Val_32 >> 8) & 0xFF
			Motor Load B	_Val_32 & 0xFF
			Motor Load B	(_Val_32 >> 8) & 0xFF


	The buffer holds 32 bytes, the rest are not used.
		Currently hold data version an maker.


	ESP8266 (2M SPIFFS)
		Sketch uses 271356 bytes (25%) of program storage space. Maximum is 1044464 bytes.
		Global variables use 28036 bytes (34%) of dynamic memory, leaving 53884 bytes for local variables. Maximum is 81920 bytes.

*/

/*	Only used by Tim	*/
//#include "Credentials.h"
//#include "Tims_Arduino_ESP8266.h"

/*	Debug	*/
//#define DEBUG

/*	Mode	*/
#define USING_SERVER
//#define USING_SERIAL


/*
  Type of connection?
  "Access Point", "Access Point with password" or "Station"

  "Access Point (AP) mode"
  This is not connected to your local network, you connect to the Network of the ESP8266.
  This means you can connect to it with your Moble Phone anywhare you are.
  You change the WiFi your Phone is connected to, to the ESP8266 WiFi.
  Then open browser to the IP of the ESP8266 control page. (we will be setting it to 192.168.50.11)
  Have your serial monitor connected when you re-set the module to confirm correct IP Address.

  "Access Point with Pasword (AP) mode"
  This is same as above, but you need a password to connect to the WiFi. (it currently is: 12345678)

  "Station (STA) mode"
  In STA mode, the ESP8266 connects to an existing WiFi network created by your wireless router.
  You will need to set the acces credentials for your local network.

  Un-Comment which way you want to connect.
*/

//#define ACCESS_POINT
//#define ACCESS_POINT_PW
#define ACCESS_POINT_STA

#include <ESP8266WiFi.h>
#include <ESP8266WebServer.h>
#include "FS.h"
#include <Wire.h>

/*
  The name of network of the ESP8266
  The Password if used

  Note!
  If changing password, make sure it is at least 8 charectors long.
  If the password is too short, it will not be updated.
  Also:
	To change WiFi Setings, make sure that the "Erase Flash" setting is set correctly in "Tools" of the Arduino IDE.
	Only use "all" if you want to remove also files in SPIFFS.

	ESP8266_SSID_AP is required if using the "Access Point (AP) mode" or "Access Point with Pasword (AP) mode".
	ESP8266_PASSWORD_AP is required if using the "Access Point with Pasword (AP) mode".

*/
const char* ESP8266_SSID_AP = "Tims Track Control";
const char* ESP8266_PASSWORD_AP = "12345678";
/*
  The name of your local network.
  The Password.

	These are required if using the "Station (STA) mode".
*/
//const char* LOCAL_SSID_STA = "Your local network name";		/*	Your local network name.		*/
//const char* LOCAL_PASSWORD_STA = "Your local network password";	/*	Your local network password.	*/
/*
  Server
*/
IPAddress local_ip(192, 168, 50, 11);   /*  IP for AP mode    */
IPAddress gateway(192, 168, 100, 1);    /*  IP for AP mode    */
IPAddress subnet(255, 255, 255, 0);     /*  IP for AP mode    */
ESP8266WebServer server(80);

#define WEB_PAGE		"/index.html"
#define TRACKS_PNG		"/Tracks.png"
#define BF1_SVG			"/BF1.svg"
#define BF2_SVG			"/BF2.svg"
#define BR1_SVG			"/BR1.svg"
#define BR2_SVG			"/BR2.svg"
#define BRL_SVG			"/BRL.svg"
#define BRR_SVG			"/BRR.svg"
#define BS_SVG			"/BS.svg"


//#define TARGET_I2C_ADDRESS	0x30    /*  0x30=48 0x60=96 0x32=50Target Address.	*/
int Target_I2C_Address = 0x30;

#define BUFF_64				64      /*  What is the longest message Arduino can store?	128 max for ESP8266	*/
#define BUFF_32				32

#define SDA_PIN 4
#define SCL_PIN 5

/*	SERIAL MESSAGES	*/
#define I2C_MESSAGE_DELAY	50
char Buffer_TX[BUFF_64];		/* message				*/
uint8_t Buffer_RX[BUFF_32];		/* message				*/
unsigned int no_data = 0;
unsigned int ByteCount;				/* size of Buffer_TX	*/
bool isComment = false;
bool procsessingString = false;
short cmd = -1;
bool slaveProcesing = false;
bool ProcsessingCommand = false;

/*	I2C Motor Driver	*/
#define MOTOR_DRIVER_ADD 0x30
char* Speed_Array = "0";
volatile byte Speed_Array_Length=1;
volatile byte i = 0;
volatile char Motor = '3';

/*	Debug	*/
long TimeNow = millis();
long Period = 1000;
long TimeOut = TimeNow + Period;

/*	====	HTML CLIENT INPUT	====	*/

/*
  Read motor command sent from client
*/
void Handle_Set_Drive_State() {

	Track_Control(server.arg("value"));

	Serial.print("Command: ");
	Serial.println(server.arg("value"));
	server.send(200, "text/plain", "OK");
	Flash_LED();

}
/*
	Movement

	Movement is controlled from two of my motor drivers.
		There are two drivers.

	The drivers take commands via the I2C.
		Arrdesses:
			Left:	0x30	(48)
			Right:	0x31	(49)

			F0		=	Stop
			R0		=	Stop
			F1		=	Forward
			R1		=	Reverse
			S800	=	speed 800
*/
void Track_Control(String command) {

	/*	Initialize Buffer_TX with NULL values (0)	*/
	memset(Buffer_TX, 0, sizeof(Buffer_TX));

	/*

	WEB
		"ST"	Both	Stop
		"LF"	Left	Forward
		"RF"	Right	Forward
		"BF"	Both	Forward
		"LR"	Left	Reverse
		"RR"	Right	Reverse
		"BR"	Both	Reverse
		"RoL"	Rotate	Right
		"RoR"	Rotate	Left

	*/

	/*	STOP	*/
	if (command == "ST") {

		Buffer_TX[0] = 'R';	/*	R	*/
		Buffer_TX[1] = '0';
		Buffer_TX[2] = ' ';
		Buffer_TX[3] = 'M';
		Buffer_TX[4] = '3';	/*	Motor Both	*/
		Buffer_TX[5] = '\r';
		Buffer_TX[6] = '\n';
		Buffer_TX[7] = 0;
		ByteCount = 8;

		SendBufferOnI2C(MOTOR_DRIVER_ADD);
	}

	/*	FORWARD	*/
	else if (command == "LF") {

		Buffer_TX[0] = 'F';	/*	F	*/
		Buffer_TX[1] = '1';
		Buffer_TX[2] = ' ';
		Buffer_TX[3] = 'S';

		for (i = 0; i < Speed_Array_Length; i++) {
			Buffer_TX[i + 4] = Speed_Array[i];
		}

		Buffer_TX[i + 4] = ' ';
		Buffer_TX[i + 5] = 'M';
		Buffer_TX[i + 6] = '2';	/*	Motor Left	*/
		Buffer_TX[i + 7] = '\r';
		Buffer_TX[i + 8] = '\n';
		Buffer_TX[i + 9] = 0;
		ByteCount = i + 10;

		SendBufferOnI2C(MOTOR_DRIVER_ADD);
	}
	else if (command == "RF") {

		Buffer_TX[0] = 'F';	/*	F	*/
		Buffer_TX[1] = '1';
		Buffer_TX[2] = ' ';
		Buffer_TX[3] = 'S';

		for (i = 0; i < Speed_Array_Length; i++) {
			Buffer_TX[i + 4] = Speed_Array[i];
		}

		Buffer_TX[i + 4] = ' ';
		Buffer_TX[i + 5] = 'M';
		Buffer_TX[i + 6] = '1';	/*	Motor Right	*/
		Buffer_TX[i + 7] = '\r';
		Buffer_TX[i + 8] = '\n';
		Buffer_TX[i + 9] = 0;
		ByteCount = i + 10;

		SendBufferOnI2C(MOTOR_DRIVER_ADD);
	}
	else if (command == "BF") {

		Buffer_TX[0] = 'F';	/*	F	*/
		Buffer_TX[1] = '1';
		Buffer_TX[2] = ' ';
		Buffer_TX[3] = 'S';

		for (i = 0; i < Speed_Array_Length; i++) {
			Buffer_TX[i + 4] = Speed_Array[i];
		}

		Buffer_TX[i + 4] = ' ';
		Buffer_TX[i + 5] = 'M';
		Buffer_TX[i + 6] = '3';	/*	Motor Both	*/
		Buffer_TX[i + 7] = '\r';
		Buffer_TX[i + 8] = '\n';
		Buffer_TX[i + 9] = 0;
		ByteCount = i + 10;

		SendBufferOnI2C(MOTOR_DRIVER_ADD);
	}

	/*	REVERSE	*/
	else if (command == "LR") {

		Buffer_TX[0] = 'R';	/*	R	*/
		Buffer_TX[1] = '1';
		Buffer_TX[2] = ' ';
		Buffer_TX[3] = 'S';

		for (i = 0; i < Speed_Array_Length; i++) {
			Buffer_TX[i + 4] = Speed_Array[i];
		}

		Buffer_TX[i + 4] = ' ';
		Buffer_TX[i + 5] = 'M';
		Buffer_TX[i + 6] = '2';	/*	Motor Left	*/
		Buffer_TX[i + 7] = '\r';
		Buffer_TX[i + 8] = '\n';
		Buffer_TX[i + 9] = 0;
		ByteCount = i + 10;

		SendBufferOnI2C(MOTOR_DRIVER_ADD);
	}
	else if (command == "RR") {

		Buffer_TX[0] = 'R';	/*	R	*/
		Buffer_TX[1] = '1';
		Buffer_TX[2] = ' ';
		Buffer_TX[3] = 'S';

		for (i = 0; i < Speed_Array_Length; i++) {
			Buffer_TX[i + 4] = Speed_Array[i];
		}

		Buffer_TX[i + 4] = ' ';
		Buffer_TX[i + 5] = 'M';
		Buffer_TX[i + 6] = '1';	/*	Motor Right	*/
		Buffer_TX[i + 7] = '\r';
		Buffer_TX[i + 8] = '\n';
		Buffer_TX[i + 9] = 0;
		ByteCount = i + 10;

		SendBufferOnI2C(MOTOR_DRIVER_ADD);
	}
	else if (command == "BR") {

		Buffer_TX[0] = 'R';	/*	R	*/
		Buffer_TX[1] = '1';
		Buffer_TX[2] = ' ';
		Buffer_TX[3] = 'S';

		for (i = 0; i < Speed_Array_Length; i++) {
			Buffer_TX[i + 4] = Speed_Array[i];
		}

		Buffer_TX[i + 4] = ' ';
		Buffer_TX[i + 5] = 'M';
		Buffer_TX[i + 6] = '3';	/*	Motor Both	*/
		Buffer_TX[i + 7] = '\r';
		Buffer_TX[i + 8] = '\n';
		Buffer_TX[i + 9] = 0;
		ByteCount = i + 10;

		SendBufferOnI2C(MOTOR_DRIVER_ADD);
	}
	/*	ROTATE	*/
	else if (command == "RoL") {

		Buffer_TX[0] = 'R';	/*	R	*/
		Buffer_TX[1] = '1';
		Buffer_TX[2] = ' ';
		Buffer_TX[3] = 'S';

		for (i = 0; i < Speed_Array_Length; i++) {
			Buffer_TX[i + 4] = Speed_Array[i];
		}

		Buffer_TX[i + 4] = ' ';
		Buffer_TX[i + 5] = 'M';
		Buffer_TX[i + 6] = '2';	/*	Motor Left	*/
		Buffer_TX[i + 7] = '\r';
		Buffer_TX[i + 8] = '\n';
		Buffer_TX[i + 9] = 0;
		ByteCount = i + 10;

		SendBufferOnI2C(MOTOR_DRIVER_ADD);

		Buffer_TX[0] = 'F';	/*	F	*/
		Buffer_TX[1] = '1';
		Buffer_TX[2] = ' ';
		Buffer_TX[3] = 'S';

		for (i = 0; i < Speed_Array_Length; i++) {
			Buffer_TX[i + 4] = Speed_Array[i];
		}

		Buffer_TX[i + 4] = ' ';
		Buffer_TX[i + 5] = 'M';
		Buffer_TX[i + 6] = '1';	/*	Motor Right	*/
		Buffer_TX[i + 7] = '\r';
		Buffer_TX[i + 8] = '\n';
		Buffer_TX[i + 9] = 0;
		ByteCount = i + 10;

		SendBufferOnI2C(MOTOR_DRIVER_ADD);

		Buffer_TX[0] = 'M';
		Buffer_TX[1] = '3';	/*	Motor Both, this is change to 3 for speed control	*/
		ByteCount = 2;
		SendBufferOnI2C(MOTOR_DRIVER_ADD);

	}
	else if (command == "RoR") {

		Buffer_TX[0] = 'F';	/*	F	*/
		Buffer_TX[1] = '1';
		Buffer_TX[2] = ' ';
		Buffer_TX[3] = 'S';

		for (i = 0; i < Speed_Array_Length; i++) {
			Buffer_TX[i + 4] = Speed_Array[i];
		}

		Buffer_TX[i + 4] = ' ';
		Buffer_TX[i + 5] = 'M';
		Buffer_TX[i + 6] = '2';	/*	Motor Left	*/
		Buffer_TX[i + 7] = '\r';
		Buffer_TX[i + 8] = '\n';
		Buffer_TX[i + 9] = 0;
		ByteCount = i + 10;

		SendBufferOnI2C(MOTOR_DRIVER_ADD);

		Buffer_TX[0] = 'R';	/*	R	*/
		Buffer_TX[1] = '1';
		Buffer_TX[2] = ' ';
		Buffer_TX[3] = 'S';

		for (i = 0; i < Speed_Array_Length; i++) {
			Buffer_TX[i + 4] = Speed_Array[i];
		}

		Buffer_TX[i + 4] = ' ';
		Buffer_TX[i + 5] = 'M';
		Buffer_TX[i + 6] = '1';	/*	Motor Right	*/
		Buffer_TX[i + 7] = '\r';
		Buffer_TX[i + 8] = '\n';
		Buffer_TX[i + 9] = 0;
		ByteCount = i + 10;

		SendBufferOnI2C(MOTOR_DRIVER_ADD);

		Buffer_TX[0] = 'M';
		Buffer_TX[1] = '3';	/*	Motor Both, this is change to 3 for speed control	*/
		ByteCount = 2;
		SendBufferOnI2C(MOTOR_DRIVER_ADD);

	}
	Motor = Buffer_TX[4];

	delay(I2C_MESSAGE_DELAY);
}
/*
  Read speed command sent from client
*/
void Handle_Set_Speed() {


	Speed_Array = new char[server.arg("value").length() + 1];
	Speed_Array_Length = server.arg("value").length();
	server.arg("value").toCharArray(Speed_Array, server.arg("value").length() + 1);

	Buffer_TX[0] = 'S';
	byte i = 0;
	for (i = 0; i < Speed_Array_Length; i++) {
		Buffer_TX[i + 1] = Speed_Array[i];
	}
	Buffer_TX[i + 1] = ' ';
	Buffer_TX[i + 2] = 'M';
	Buffer_TX[i + 3] = Motor;
	Buffer_TX[i + 4] = '\r';
	Buffer_TX[i + 5] = '\n';
	Buffer_TX[i + 6] = 0;
	ByteCount = i + 8;

	SendBufferOnI2C(MOTOR_DRIVER_ADD);
	delay(I2C_MESSAGE_DELAY);

	Serial.print("Command: ");
	Serial.println(server.arg("value"));
	server.send(200, "text/plain", "OK");
	Flash_LED();

}
/*
  HTTP request: 404
*/
void Handle_Not_Found() {
	Serial.println("Error 404 not found");
	server.send(404, "text/plain", "Not found");
}

/*	====	SERIAL INPUT	====	*/

/*
	Read Data in Serial Buffer if available.
*/
void ReadSerial() {
	/*
		Holder
	*/
	char c;
	/*
		Read in characters if available.
	*/
	if (Serial.available() > 0) {
		c = Serial.read();
		no_data = 0;
		/*
			Chech for newlines.
		*/
		if (c != '\r' || c != '\n') {
			/*
				Check for comments.
					These are used in G-Code.
			*/
			if (c == '(' || c == ';') {
				isComment = true;
			}
			/*
				If we're not in "isComment" mode, add it to our array.
			*/
			if (!isComment) {
				Buffer_TX[ByteCount++] = c;
			}
			/*
				End of isComment - start listening again.
			*/
			if (c == ')') {
				isComment = false;
			}
		}
	}
	else {
		no_data++;
		delayMicroseconds(100); // 100
		/*
			Process any code that has been recived
		*/
		if (ByteCount && (c == '\n' || c == '\r' || no_data > 100)) {
			no_data = 0;
			ByteCount--;

#ifdef DEBUG
			Serial.println(Buffer_TX);
			delay(50);
#endif    /*  DEBUG	*/

			procsessingString = true;
			processCommand();
			init_process_string();
		}
	}

}
/*
	Set ready for next command.
*/
void init_process_string() {

	for (byte i = 0; i < BUFF_64; i++) { Buffer_TX[i] = 0; }
	ByteCount = 0;
	procsessingString = false;
	isComment = false;
	cmd = -1;
	Wire.flush();
	Serial.flush();
	Serial.println("ok");
	delay(4);
}
/*
	Change command numbers to a long.
*/
long Parse_Number(char code, long val) {
	/*
		start at the beginning of Buffer_TX.
	*/
	char* ptr = Buffer_TX;
	/*
	  Go char to char through string.
	*/
	while ((long)ptr > 1 && (*ptr) && (long)ptr < (long)Buffer_TX + ByteCount) {
		/*
			if you find code as you go through string.
		*/
		if (*ptr == code) {
			/*
				convert the digits that follow into a long and return it.
			*/
			return atol(ptr + 1);
		}
		/*
			take a step from here to the next char after the next space.
		*/
		ptr = strchr(ptr, ' ') + 1;
	}
	/*
		If the end is reached and nothing found, return val.
	*/
	return val;
}
/*
	Process Commands.
*/
void processCommand() {

	uint32_t _Val = 0;
	uint8_t _Flag1 = 0;
	uint8_t _Flag2 = 0;

	/*	Get I2C Address if given. (defalt 0x30 or last sent)	*/
	Target_I2C_Address = Parse_Number('D', Target_I2C_Address);

	/*	get start of Buffer_TX (see what the command starts with)	*/
	char* ptr = Buffer_TX; // 

	/*
		======================
		Chose GET, Process or SEND
		======================
	*/
	if (*ptr == 'X') {
		/*	GET	*/
		int _numberOfBytes = Parse_Number('X', -1);
		if (_numberOfBytes == 0) {
			_numberOfBytes = BUFF_32;
		}

		/*	Clear Buffer	*/
		for (size_t i = 0; i < BUFF_32; i++) {
			Buffer_RX[i] = 0;
		}

		Wire.requestFrom(Target_I2C_Address, _numberOfBytes);
		delayMicroseconds(5);

		if (Wire.available()) {
			/*	Read Buffer	*/
			for (size_t i = 0; i < _numberOfBytes; i++) {
				uint8_t C = Wire.read();
				Buffer_RX[i] = C;
				//Serial.print(C);
				//Serial.print(", ");
			}
			//Serial.println();
		}
		/*	Buffer in Binary	*/
		if (_numberOfBytes > 7) {
			for (size_t i = BUFF_32; i > 0; i--) {

				Serial.print("Buffer_RX[");
				Serial.print(i - 1);
				Serial.print("] \tBIN = ");
				Serial.println(Buffer_RX[i - 1], BIN);
			}
		}


		/*
			===============
			Use and Format Info
			===============
		*/

		/*	Slave_Buffer_Tx[7] = Flags	*/
		_Flag1 = Buffer_RX[0];
		if (Buffer_RX[6] == 0) {
			Serial.println();
			Serial.print("No Address ");
			Serial.print(Target_I2C_Address, DEC);
			Serial.print(" (0x");
			Serial.print(Target_I2C_Address, HEX);
			Serial.print(") found.");
			Serial.println();
		}
		else {
			Serial.println();
			Serial.println("Formated:");
			Serial.println();

			/*	Currrent Possition	*/
			//_Val = Buffer_RX[5];
			//_Val = _Val << 0x08;
			_Val |= Buffer_RX[4];
			_Val = _Val << 0x08;
			_Val |= Buffer_RX[3];
			_Val = _Val << 0x08;
			_Val |= Buffer_RX[2];
			Serial.print("Currrent Position\tDEC = ");
			_Flag1 = (Buffer_RX[0] & 1);
			if (_Flag1 == 1) { Serial.print("-"); }
			else { Serial.print(" "); }
			Serial.println(_Val, DEC);

			/*	Limit Switches	*/
			_Flag2 = (Buffer_RX[1] & 1);
			if (_Flag2 == 1) { Serial.println("MIN Stop Hit"); }
			else { Serial.println("MIN OK"); }
			_Flag2 = (Buffer_RX[1] & 2);
			if (_Flag2 == 2) { Serial.println("MAX Stop Hit"); }
			else { Serial.println("MAX OK"); }

			if (_numberOfBytes > 7) {

				/*	My_I2C_Address		*/
				Serial.print("I2C Address\t\t\tDEC =  ");
				Serial.print(Buffer_RX[6], DEC);
				Serial.print("(HEX = 0x");
				Serial.print(Buffer_RX[6], HEX);
				Serial.println(")");

				/*  I2C Speed  */
				Serial.print("I2C Speed\t\t\tDEC =  ");
				_Flag2 = (Buffer_RX[1] & 4);
				if (_Flag2 == 4) { Serial.println("400000"); }
				else { Serial.println("100000"); }


				/*	Motor_Slowdown		*/
				_Val = Buffer_RX[8];
				_Val = _Val << 0x08;
				_Val |= Buffer_RX[7];
				Serial.print("Motor Slowdown\t\tDEC =  ");
				Serial.println(_Val);

				/*	MaxPossition		*/
				//_Val = Buffer_RX[12];
				//_Val = _Val << 0x08;
				_Val = Buffer_RX[11];
				_Val = _Val << 0x08;
				_Val |= Buffer_RX[10];
				_Val = _Val << 0x08;
				_Val |= Buffer_RX[9];
				Serial.print("Max Possition    \tDEC = ");
				_Flag1 = (Buffer_RX[0] & 2);
				if (_Flag1 == 2) { Serial.print("-"); }
				else { Serial.print(" "); }
				Serial.println(_Val, DEC);

				/*	MinPossition		*/
				//_Val = Buffer_RX[16];
				//_Val = _Val << 0x08;
				_Val = Buffer_RX[15];
				_Val = _Val << 0x08;
				_Val |= Buffer_RX[14];
				_Val = _Val << 0x08;
				_Val |= Buffer_RX[13];
				Serial.print("Min Possition    \tDEC = ");
				_Flag1 = (Buffer_RX[0] & 4);
				if (_Flag1 == 4) { Serial.print("-"); }
				else { Serial.print(" "); }
				Serial.println(_Val, DEC);

				/*	Station F		*/
				//_Val = Buffer_RX[20];
				//_Val = _Val << 0x08;
				//_Val |= Buffer_RX[19];
				//_Val = _Val << 0x08;
				_Val = Buffer_RX[18];
				_Val = _Val << 0x08;
				_Val |= Buffer_RX[17];
				Serial.print("Station Forward\t\tDEC = ");
				_Flag1 = (Buffer_RX[0] & 8);
				if (_Flag1 == 8) { Serial.print("-"); }
				else { Serial.print(" "); }
				Serial.println(_Val, DEC);

				/*	Station R		*/
				//_Val = Buffer_RX[24];
				//_Val = _Val << 0x08;
				//_Val |= Buffer_RX[23];
				//_Val = _Val << 0x08;
				_Val = Buffer_RX[22];
				_Val = _Val << 0x08;
				_Val |= Buffer_RX[21];
				Serial.print("Station Reverse\t\tDEC = ");
				_Flag1 = (Buffer_RX[0] & 16);
				if (_Flag1 == 16) { Serial.print("-"); }
				else { Serial.print(" "); }
				Serial.println(_Val, DEC);

				/*	HasFlags		*/
				_Flag1 = (Buffer_RX[0] & 32);
				if (_Flag1 == 32) { Serial.println("\tHasMAX       = true"); }
				else { Serial.println("\tHasMAX       = false"); }
				_Flag1 = (Buffer_RX[0] & 64);
				if (_Flag1 == 64) { Serial.println("\tHasMIN       = true"); }
				else { Serial.println("\tHasMIN       = false"); }
				_Flag1 = (Buffer_RX[0] & 128);
				if (_Flag1 == 128) { Serial.println("\tHasStation   = true"); }
				else { Serial.println("\tHasStation   = false"); }

				/*	Motor Speed Reduction	*/
				Serial.print("Motor Speed Reduction = ");
				Serial.print(Buffer_RX[25]);
				Serial.println("%");

				/*	Tim			*/
				for (size_t i = 29; i < 32; i++) {
					Serial.print((char)Buffer_RX[i]);
				}
				Serial.println();

			}

			delayMicroseconds(5);
		}
	}
	else if (*ptr == 'P') {

	}
	else {
		/*	SEND	*/
		ProcsessingCommand = true;
		Wire.flush();
		SendBufferOnI2C(Target_I2C_Address);
		delay(4);
		ProcsessingCommand = false;

	}
}
/*
	Send Recived Commands on to a Device on the I2C bus.
*/
void SendBufferOnI2C(int I2C_address) {

	Wire.beginTransmission(I2C_address);	/*	Connect with device at I2C_address.	*/
	Wire.write('#');						/*	Send garbage for the first byte of data that will be ignored.	*/
	Wire.write(Buffer_TX, ByteCount);			/*	Send Buffer_TX.						*/
	Wire.endTransmission();					/*	Disconnect.							*/

#ifdef DEBUG
	Serial.print("I2C_address 0x");
	Serial.print(I2C_address, HEX);
	Serial.print(" (");
	Serial.print(I2C_address);
	Serial.print(")");
	Serial.print("\t Buffer_TX ");
	Serial.print(Buffer_TX);
	Serial.print("\t ByteCount ");
	Serial.println(ByteCount);
	delay(50);
#endif  /*  DEBUG	*/

}
/*
	I2C Request Data
*/
void Wire_Request() {

}

/*	Debug	*/
void Flash_LED() {

	digitalWrite(LED_BUILTIN, !digitalRead(LED_BUILTIN));
	delay(100);
	digitalWrite(LED_BUILTIN, !digitalRead(LED_BUILTIN));
	delay(100);
	digitalWrite(LED_BUILTIN, !digitalRead(LED_BUILTIN));
}
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
void loop() {

#ifdef USING_SERVER

	/*
		Handle HTTP requests.

			This should be the only thing here.
			All actions should be run through commands to the server,
			by requests from the client (Web Page).
	*/
	server.handleClient();

#else

	/*
		Tick - Tock
	*/
	TimeNow = millis();
	/*
		Get next command when finish current command.
	*/
	if (!procsessingString) { ReadSerial(); }

	if (TimeNow > TimeOut) {
		TimeOut = TimeNow + Period;
		digitalWrite(LED_BUILTIN, !digitalRead(LED_BUILTIN));
	}

#endif // USING_SERVER

}

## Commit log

2024-07-07 Add project files.
    [My laser Cut Paste Mask (Kurf Adjusted).dxf, My laser Cut Paste Mask.dxf, Tims_I2C_Dual_Motor_Driver-B_Cu.dxf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]
2024-07-07 Clean up Unwanted
    [Tims_I2C_Dual_Motor_Driver-B_Cu.gbr, Tims_I2C_Dual_Motor_Driver-B_Mask.gbr, Tims_I2C_Dual_Motor_Driver-B_Paste.gbr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]
2024-07-07 Clean up
    [My laser Cut Paste Mask (Kurf Adjusted).dxf, My laser Cut Paste Mask.dxf, Tims_I2C_Dual_Motor_Driver-B_Cu.dxf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]
2024-07-09 Add PCBWay
    [PCBWay_bom.csv, PCBWay_positions.csv]
2024-08-12 Update LED Resistors.
    [Tims_I2C_Dual_Motor_Driver.kicad_sch]
